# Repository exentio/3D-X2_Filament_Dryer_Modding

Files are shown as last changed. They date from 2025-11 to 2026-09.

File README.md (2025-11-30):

# 3D-X2 Filament Dryer Modding

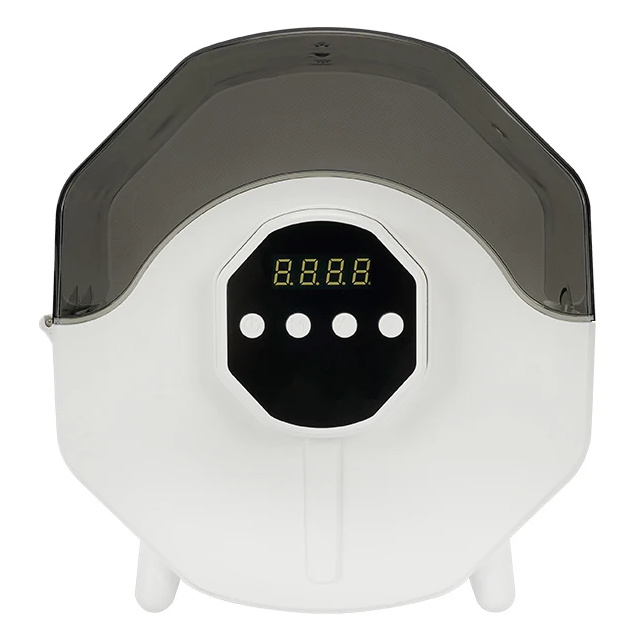
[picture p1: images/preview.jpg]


This is a filament dryer that can be found for cheap on Aliexpress, by word
salad brands like Kingroon and Keepang ([example](https://aliexpress.com/item/1005009156634726.html)).  

I paid €27,48 for mine after discounts and I bought it with the intention to
build a custom PCB for it with a better temperature sensor and an ESP32, sure
to be able to reuse the fan, heater, and other hardware like the bearing and
rods to make the filament roll when pulled by the printer.  

What I wasn't expecting was that the PCB would've been so simple to
reverse-engineer, and to find an STM32 (precisely, STM32G030F6P6), not only
with SWD pins exposed, but also with no flash protection whatsoever.  

The goal of this repo is to document my progress with modding this dryer and
make it available to everyone.  

**In case of possible variants being sold, double check the PCB images and
things like IC models from the schematics. The original firmware dump has been
tested and is working, BUT dump your own too, in case of hardware variants.  
I take no responsibility for broken hardware.**

### Hardware specifications and other details

+ Rated voltage/power: 24V 2A (48W)  
+ Included power supply: 24V 2.5A (mine came with this, may vary)  
+ Timer settings (stock firmware): 0.5 to 24 hours with a continuous on mode  
+ Heating temperatures (stock firmware): 50/60/70°C  
+ Heating element: polyimide flexible heater, glued onto a curved metal sheet
sitting under the filament roll  
+ Fan: 24V 40mm blower (actual fan diameter 30mm)  
+ Sensors:
  + SMD thermistor, likely 100KΩ rated value, soldered in the middle of the heater  
  + 2-pin relative humidity sensor glued on the bottom of the dryer, likely a
  CJ-HR31D resistive humidity sensor  
+ Other hardware info:  
  + Bearing sizes: 11mm outer diameter, 4mm internal hole, 4mm thickness  
  + Filament rolling rods: 6mm diameter, 4mm diameter taper at ends, 83mm long
  without taper, 91mm with taper (4mm on each side)

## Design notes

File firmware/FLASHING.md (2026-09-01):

# Firmware flashing

To flash the firmware, you'll need an SWD programmer, I'm using an ST-Link V2
and I can't guarantee that anything else will work, but you can try.  

The pinout of the headers on the back of the PCB is as follows:  

| Pin | Function |
|-----|---|
| 1 | SWDIO |
| 2 | VCC (3.3V)  |
| 3 | SWCLK/BOOT0 |
| 4 | GND |
| 5 | nRST |
| 6 | GND |

Keep in mind, the order is right to left, top to bottom, as marked on the
silkscreen.  

You'll need STLINK Tools [from this repo](https://github.com/stlink-org/stlink).  

To dump the firmware: `st-flash read firmware.bin 0x0 32k`  
It's recommended to dump the firmware multiple times and compare the checksums
to make sure you have a working firmware dump.  

To flash the firmware: `st-flash --reset --format binary write firmware.bin 0x8000000`  

### Unbricking

Should you ever find yourself unable to flash (happens with Arduino), here's
what works for me.  

Connect SWD as normal, and connect the nRST pin to GND.  
Get the flash command ready in a terminal or your favorite tool, but wait
before launching the flash.  
In another terminal, run this command, it will fail saying it can't find any chip id:
`st-flash --reset --connect-under-reset --format binary write original_firmware_dump.bin 0x08000000`  
Then launch the flash command quickly, as soon as you disconnect the reset pin from GND.

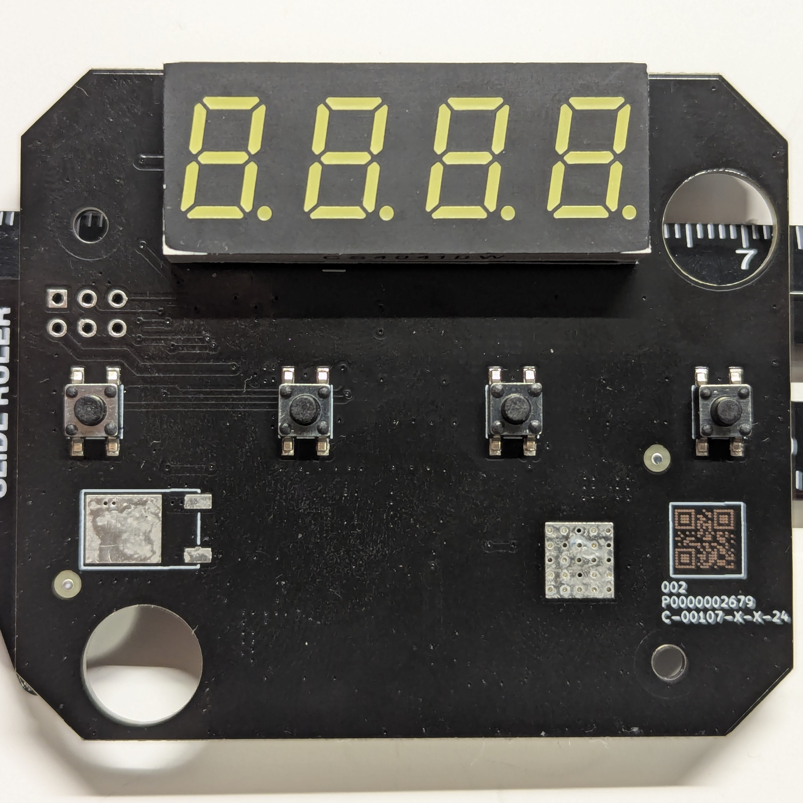
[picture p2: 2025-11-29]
images/og_pcb_front.jpg

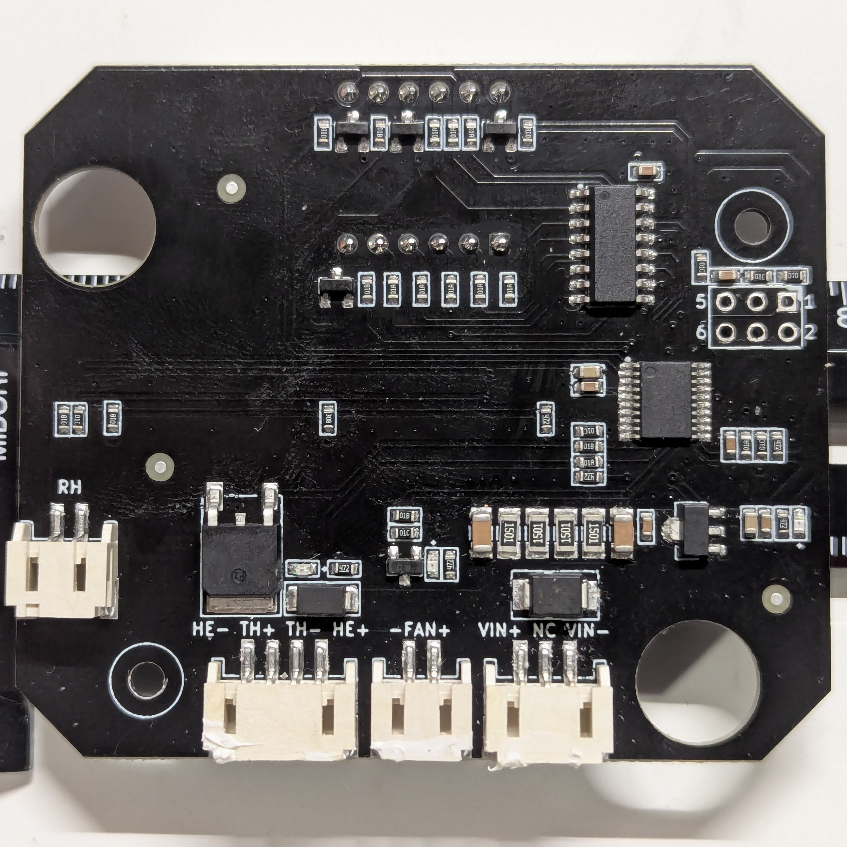
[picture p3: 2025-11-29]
images/og_pcb_back.jpg

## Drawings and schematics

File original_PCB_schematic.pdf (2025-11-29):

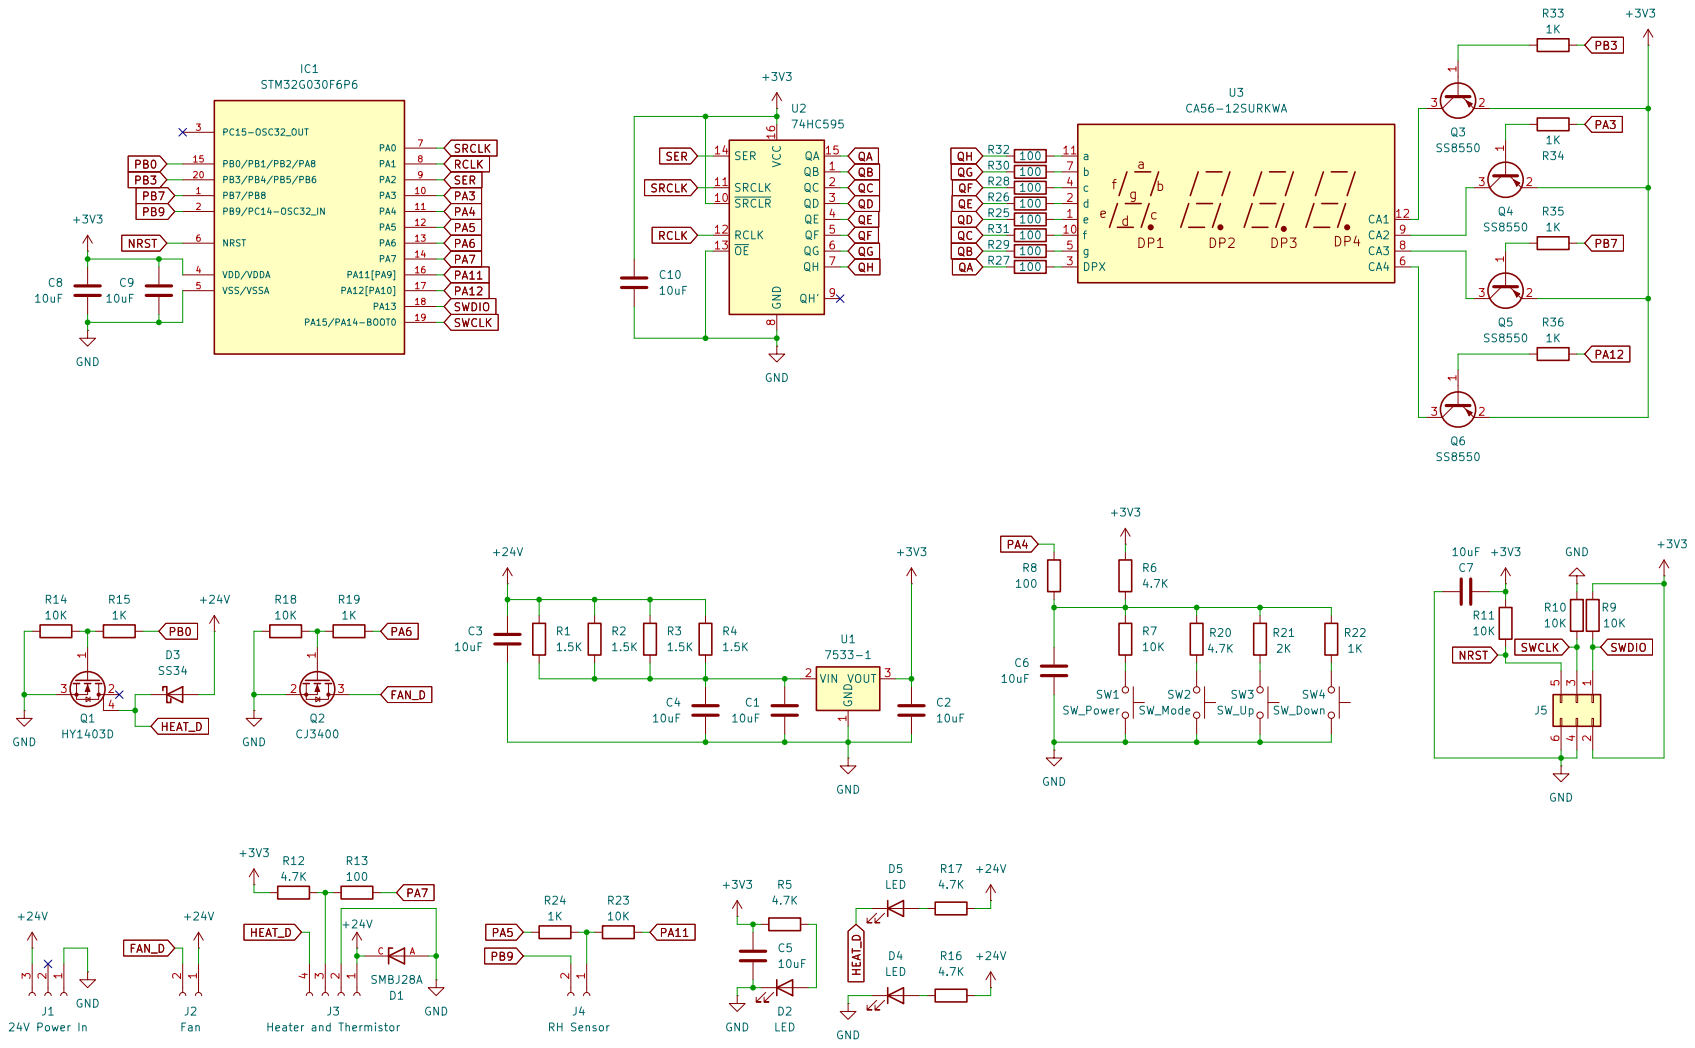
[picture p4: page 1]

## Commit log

2025-11-29 Added PDF version of schematics
2025-11-30 Readme update
    [3D-X2_Filament_Dryer_Modding.kicad_sch]
